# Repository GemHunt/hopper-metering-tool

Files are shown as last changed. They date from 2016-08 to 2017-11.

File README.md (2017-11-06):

# hopper-metering-tool
Uses an Arduino to meter coins out of an Suzohapp MKII Cube Hopper at an exact interval. 

This works great and is used in production.

Tasks for next build:
  * Post a picture of the current build.
  * Test if the whole hopper can be turned off instead of just the motor. 
  * It would be nice to print a circuit board for this.

***

It gets input from the cube hopper's open-collector output time the power on the motor. 

A general page on an open-collector circuit details:  http://www.evilmadscientist.com/2012/basics-open-collector-outputs/

Hopper Wiring Notes:
* Only 5 wires need to connect to the hopper: (Pretend it does not have power like a Ryedale) 
* A	6# (Signal) 
* B 	8# (Ground) 
* C	9# (12V Positive) 
* D	Black from the motor (Positive: Hopper is wired backwards from the factory)
* E	Red from the motor (Ground: Hopper is wired backwards from the factory)
* The motor is no longer connected to the hopper control board. 

Arduino Takes 12V in with the Barrel jack 
* A	To Arduino Pin 0
* B 	Ground on the Arduino
* 	Solenoid NC
* 	Ground PIN on the Relay board
* 	E (Ground - Red on Motor) 
* C	VIN on the Arduino
* 	Solenoid NO	
* E	Solenoid COM

Wire:
* 5V Arduino To 4700 Ohm then Arduino Pin 0

Relay Module Board Controls:
* (The input pins must be pulled to ground for the relay to turn on. )
* VIN to 5V on the Arduino
* Input 2 to PIN 9 on the Arduino
* Ground to Ground

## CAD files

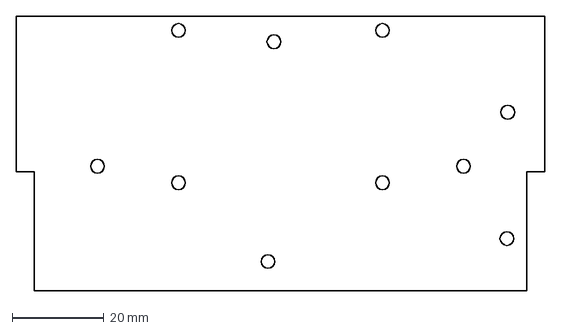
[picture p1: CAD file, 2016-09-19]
hopper-arduino-base.dxf
115.5 x 60.0 mm

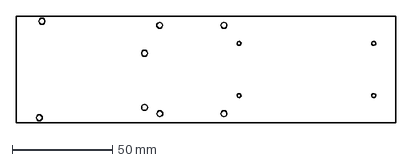
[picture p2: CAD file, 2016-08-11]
unoRelayHolePattern.dxf
188.9 x 53.0 mm

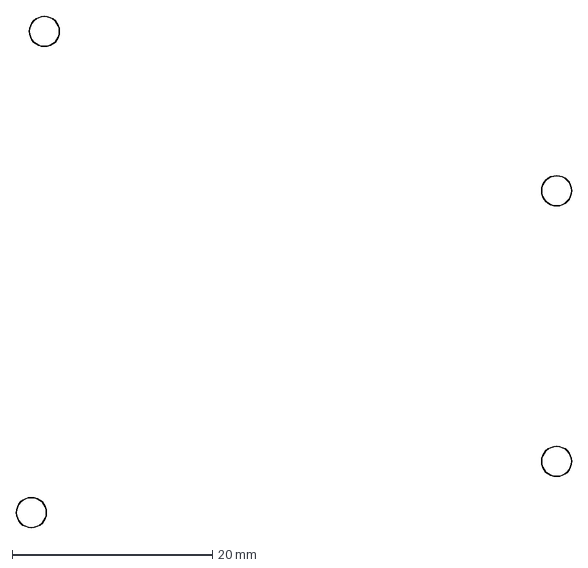
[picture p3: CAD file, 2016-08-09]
unoCloneHolePattern.dxf
55.4 x 51.0 mm

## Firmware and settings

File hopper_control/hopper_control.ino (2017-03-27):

int hopperSignalPin = A0;
int motorPin = 9;
unsigned long coinEnterTime = 0;
unsigned long coinExitTime = 0;
unsigned long coinPassTime = 0;
//OK just once and stop for now:
unsigned long betweenTime = 90000000;
unsigned long pennyCount = 0;


void setup() {
  // put your setup code here, to run once:
  Serial.begin(115200);
  pinMode(hopperSignalPin, INPUT);
  pinMode(motorPin, OUTPUT);

  digitalWrite(motorPin,LOW);
}

void loop() {
  int signalReading = analogRead(hopperSignalPin);
    Serial.print("sig");
    Serial.println(signalReading);
  if (signalReading < 20) {
    if (coinPassTime == 0){
      coinPassTime = 1;
      coinEnterTime = millis();
      Serial.print("Enter");
      Serial.println(coinEnterTime);
      delay(10);
    }
  }
  
  if (signalReading >= 20){
    if (coinPassTime != 0){
      coinPassTime = millis() - coinEnterTime;
      Serial.print("Pass");
      Serial.println(coinPassTime);
      if (coinExitTime == 0){
        coinPassTime = 1;
        coinExitTime = millis();
        Serial.print("Exit");
        Serial.println(coinExitTime);
      }
      if (coinExitTime >= 20){
        digitalWrite(motorPin,HIGH);
        delay(betweenTime - coinPassTime);
        coinExitTime = 0;
        coinPassTime = 0;
        pennyCount ++;
        Serial.print("$");
        Serial.println(pennyCount);
        digitalWrite(motorPin,LOW);
      }    
    }
  }
}

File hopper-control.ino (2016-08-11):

int hopperPin = 8;
int stopMotorPin = 9;
int inhibitMotorPin = 9;
unsigned long startTime;
unsigned long delayTime;

int offDelayTime = 90;

int betweenTime = 1000;
int pennyCount = 0;
void setup() {
  // put your setup code here, to run once:
  Serial.begin(9600);
  pinMode(hopperPin, INPUT);
  pinMode(stopMotorPin, OUTPUT);
  pinMode(inhibitMotorPin, OUTPUT);
  betweenTime -= offDelayTime;
  startTime = 0;
  
  
}

void loop() {


  //for timing
  if(millis()>60000){
    Serial.println("Done");
    while(1){
      delay(1000);
    }  
  }


  
 
  digitalWrite(stopMotorPin,HIGH);

  
  while(!digitalRead(hopperPin)){

    delay(offDelayTime);
    
    digitalWrite(stopMotorPin,LOW);
    
    delayTime = betweenTime-(millis()-startTime);
    
    if(delayTime > betweenTime + offDelayTime){
      delayTime = 0;  
    }
    
    Serial.print("Delay: ");
    Serial.println(delayTime);
    
    delay(delayTime);
    startTime = millis();
    pennyCount ++;
    Serial.print("Pennies: ");
    Serial.println(pennyCount);
    
  
    
    
  }
  
  

}

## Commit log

2016-08-11 add pictures, updated hole pattern, arduino code
    [unoRelayHolePattern.dxf]
2016-09-19 Added laser cut bases to hopper
    This makes things much cleaner. They hold the ardunio and relay board.
    [hopper-arduino-base.dxf]
2016-09-20 Added wiring details
2017-03-27 Made it so the hopper only dispenses one coin. The control is now using reset to dispense.
    [hopper_control.ino]
